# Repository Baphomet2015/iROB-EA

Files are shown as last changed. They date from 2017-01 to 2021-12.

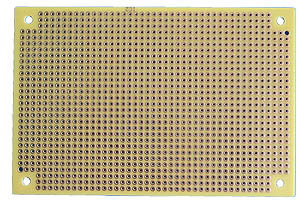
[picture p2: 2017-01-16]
Doc/Documentacion/Ilustraciones/wrapping_04.jpg

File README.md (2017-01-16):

# iROB-EA
Proyecto de Robot Movil Autónomo

Se trata de un Robot Móvil Autónomo todo terreno para exploración de entornos abiertos.

Dos modos básicos de funcionamiento:

 1. Modo autónomo con capacidad de ejecutar tareas de exploración programadas.
 
 2. Modo guiado recibiendo instrucciones en remoto.

Está equipado entre otros con los siguientes sensores:

 1. Estación Meteorológica.
 2. Sensores de Temperatura por infrarrojos.
 3. Sensores de ultrasonidos.
 4. Acelerómetro, brújula, sensores de posicion X-Y-Z.
 5. Camara video HD , movimiento X-Y.
 6. Microfonos.
 7. GPS

Conectividad y Sw básico:

 1. Conectividad Internet.
 2. Servidor web embebido.

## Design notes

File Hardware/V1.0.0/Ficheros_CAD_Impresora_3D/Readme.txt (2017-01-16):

Notas sobre el diseño de las piezas CAD utilizadas en iROB-EA

1) Para el diseño de estas piezas se ha utilizado el software FreecAD.

Descarga:	http://www.freecadweb.org/
Tutorial:	http://spainlabs.com/wiki/index.php?title=Tutorial_r%C3%A1pido_de_FreeCad
		http://www.iearobotics.com/wiki/index.php?title=Dise%C3%B1o_de_piezas_con_Freecad

2) Para la impresion de las piezas se ha utilizado una impresora 3D xyzprinting, modelo da Vinci 1.0.A

Web:		http://www.xyzprinting.com
Producto:	http://us.xyzprinting.com/us_es/Product/da-Vinci-1.0

Todas las piezas se han impreso utilizando como material de impresión plástico, PLA.

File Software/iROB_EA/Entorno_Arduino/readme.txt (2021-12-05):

iROB-EA, Librerías específicas Arduino del proyecto

LIBRERIAS

las carpetas contenidas en este directorio contienen las librerias especificas y 
necesarias para compilar la aplicación que se ejecuta en el Arduino MEGA2560.
Se deben copiar tal cual estan en el directorio "libraries" de la versión de IDE Arduino
que se esté utilizando.

Atención:
Es posible que alguna de estas librerias Ya exista en el directorio de "libraries" del IDE,
en cuyo caso es recomendable reemplazar la que exista por la que se encuentra aquí.

ENTORNO ARDUINO

La versión del IDE de Arduino con la que se ha desarrollado el SW es la 1.8.12

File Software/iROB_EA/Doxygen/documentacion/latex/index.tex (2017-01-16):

Proyecto\+: i\+R\+O\+B-\/\+EA 

\begin{DoxyDate}{Date}
Fecha\+: Abril 2015 
\end{DoxyDate}
\begin{DoxyAuthor}{Author}
A\+AL
\end{DoxyAuthor}
\begin{DoxyRemark}{Remarks}
Hardware Arduino M\+E\+GA 2560~\newline
 
\end{DoxyRemark}
\begin{DoxyVersion}{Version}
Versión de SW 1.\+0 

Versión de I\+DE Arduino\+: 1.\+6.\+4
\end{DoxyVersion}
{\bfseries Leitmotiv\+:}~\newline
 \char`\"{}\+Toda Bestia necesita un Cerebro...\char`\"{}, Dr. Frankenstein, en su laboratorio~\newline
 \char`\"{}¡\+Larga y próspera vida!.\char`\"{}, Sr. Spock~\newline

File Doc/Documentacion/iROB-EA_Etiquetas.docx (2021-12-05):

CN1 CN1 CN1 CN2 CN2 CN2 CN3 CN3 CN3 CN4 CN4 CN4 CN5 CN5 CN5 CN6 CN6 CN6 | CN7 CN7 CN7 CN8 CN8 CN8 CN9 CN9 CN9 CN10 CN10 CN10 CN11 CN11 CN11 CN12 CN12 CN12
CN13 CN13 CN13 CN14 CN14 CN14 CN15 CN15 CN15 CN16 CN16 CN16 CN17 CN17 CN17 CN18 CN18 CN18 | CN19 CN19 CN19 CN20 CN20 CN20 CN21 CN21 CN21 CN22 CN22 CN22 CN23 CN23 CN23 CN24 CN24 CN24
+ CN16 - - CN17 + + CN16 - - CN17 + P N P N | +12VDC ◄-- RS-232 Depuración USB programación
RX1 RX2 RX3 RX4 TX1 TX2 TX3 TX4 X Y SRVX SRVX X Y SRVY SRVY | U1 U1 U1 U4 U2 U2 U3 U3 U3 U4 U4 U4 U5 U5 U5
P1 P2 P3 P4 P1 P2 P3 P4 P1 P2 P3 P4 P1 P2 P3 P4 P1 P2 P3 P4 | U6 U6 U6 U7 U7 U7 U8 U8 U8 U9 U9 U9 U10 U10 U10
U11 U11 U11 U12 U12 U12 U13 U13 U13 U14 U14 U14 U15 U15 U15 | CARGADOR FIRMWARE 9DOF Razor IMU •GND

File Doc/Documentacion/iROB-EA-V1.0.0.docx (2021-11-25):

# xx

aAL

Versión 1.0, ENERO 2021

# 1 índice

# 2 objetivo

El objeto de este documento es describir un robot autónomo explorador que se denominará a lo largo de todo el documento iROB-EA.

## 2.1 glosario de términos

- iROB-EA. internet ROBobot Explorador Autónomo. Robot descrito en el presente documento.
- UF_xxx. Unidad Funcional.

El término concreto será del tipo UF_xxx dónde “xxx” serán tres caracteres alfanuméricos que identifican la Unidad Funcional.

- SS_xxx. Sub Sistema.

El término concreto será del tipo SS_xxx dónde “xxx” serán tres caracteres alfanuméricos que identifican el Subsistema.

# 3 introducción

Se propone el diseño de un robot autónomo cuya misión será explorar y recabar información del entorno que le rodea.

A lo largo del presente documento se aportará toda la información necesaria para comprender el funcionamiento del iROB-EA así como para su construcción a nivel hardware, en tanto que la información relacionada con el software necesario para su correcto funcionamiento se encuentra fuera de este documento, formando parte de la documentación general del proyecto.

Así mismo, si bien este documento recoge la documentación de detalle del hardware del iROB-EA la construcción “final” del mismo queda a la elección del lector, por lo que no se darán indicaciones de cómo se debe construir una parte concreta u otra, si el lector decide por ejemplo utilizar un chasis de otro tipo quedará pues a su elección.

# 4 especificaciones

Se definen las siguientes especificaciones para el iROB-EA.

# 5 arquitectura

En este capítulo se recoge la arquitectura del iROB-EA.

La Arquitectura del iROB-EA se estructura en base a xx Unidades Funcionales (UFs).

Cada una de estas unidades está a su vez formada por varios Subsistemas que tienen relación directa entre ellos, estos subsistemas en conjunto proveen la funcionalidad que la UF soporta.

Un subsistema debe ser entendido como un circuito o conjunto de ellos que operan bien de forma autónoma o controlados por una aplicación o software.

Algunos subsistemas son simples circuitos mientras que otros pueden tener más entidad.

La siguiente ilustración muestra las distintas UFs que conforman la arquitectura y su relación entre ellas.

Ilustración 1. Arquitectura iROB-EA.

Como se puede apreciar existen xx UFs claramente diferenciadas cuya misión se describe a continuación.

## 5.1 UF_SYS

Unidad Funcional de SYStema.

Esta UF es la encargada de proveer los siguientes servicios:

- Gestión de sensores.
- Gestión de actuadores.
- Interfaz de depuración (debug).
- Gestión de alimentación subsistemas.
- Implementación del mecanismo de reacciones básicas.

Esta UF implementa el “BIOS” del iROB-EA soportando todas las funciones de bajo nivel tales como gestión de sensores y actuadores, obteniendo de los mismos la información que facilitan y poniéndola a disposición de la UF_APL que es la encargada de ejecutar los programas y aplicaciones de alto nivel del iROB-EA.

Una tarea importante llevada a cabo en esta UF es la de soportar un mecanismo denominado de reacciones básicas, por el cual la UF_SYS responde de forma automática ante determinadas situaciones reconocidas en base a la información obtenida de los diferentes sensores. Este mecanismo funciona de forma similar al que provoca los actos reflejos en los seres vivos.

Existen situaciones de alta prioridad ante las que es preciso actuar de forma inmediata dado que son potencialmente peligrosas para la integridad del iROB-EA, ante cualquiera de estas situaciones la UF_SYS procede a asegurar la integridad del iROB-EA para posteriormente comunicar la aparición de esta situación a la UF_APL.

La UF_SYS está formada por un único subsistema:

- SS_SYS. Subsistema principal de la UF_SYS.

### 5.1.1 SS_SYS

Este subsistema es el único componente de la UF_SYS y está implementado entorno a un Arduino MEGA2560,

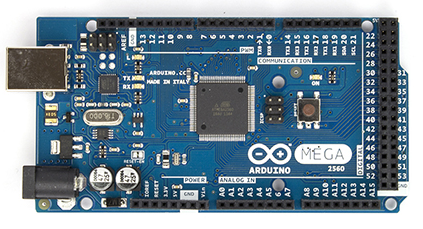
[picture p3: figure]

El modelo MEGA2560 posee entre otras, las siguientes características,

Microcontrolador | ATmega2560
Tensión de operación | 5V
Digital I/O Pins | 54 (15 de ellos soportan salida PWM)
Analógicos I/O Pins | 16
Corriente DC por I/O | 40 mA
Memoria Flash | 256 KB (8 KB usados por el bootloader)
SRAM | 8 KB
EEPROM | 4 KB
Clock | 16 MHz

Para más información consultar la web del fabricante,

http://arduino.cc/en/Main/ArduinoBoardMega2560

Así mismo se encuentra disponible en numerosos sitios online, entre otros,

http://tienda.bricogeek.com/arduino/306-arduino-mega-2560.html

https://www.sparkfun.com/products/11061

http://www.cooking-hacks.com/arduino-mega-2560

Como se ha comentado, este subsistema es el encargado de gestionar todos los sensores y actuadores del iROB-EA.

Este subsistema se comunica utilizando los puertos serie que incorpora el ArduinoMEGA2560 manteniendo conexión con los siguientes elementos:

- Exterior.

Puerto de comunicación serie RS-232 con el exterior para tareas de depuración y test, este puerto está presente en el conector exterior de DEBUG, soportado a través del SS_DBG de la unidad funcional UF_ENE, que convierte los niveles de Transmisión/Recepción a RS-232.

- UF_APL.

Puerto de comunicación serie con la UF_APL que es la unidad funcional encargada de ejecutar las aplicaciones que proveen de funcionalidad al iROB-EA.

## 5.2 UF_APL

Unidad Funcional de APLicaciones.

Esta UF es la encargada de proveer los siguientes servicios:

- xx
- xx
- xx

La UF_APL está formada por los siguientes subsistemas:

- xx
- xx
- xx

## 5.3 UF_ENE

Unidad Funcional de ENErgía.

Esta UF es la encargada de proveer los siguientes servicios:

- Encendido y Apagado general del iROB-EA.
- Recarga de baterías y obtención de información acerca del estado general de las mismas.
- Encendido y apagado de elementos y subsistemas.
- Alimentación y comunicaciones en modo pruebas (DEBUG).
- Watchdog.

La UF_ENE está formada por los siguientes subsistemas:

- SS_POW. Este subsistema es el encargado del encendido y apagado (power On/Off) del iROB-EA.
- SS_BAT. Este subsistema permite generar las tensiones de alimentación, recargar las baterías y operaciones asociadas con las mismas.
- SS_CNX. Subsistema que permite activar/desactivar la alimentación suministrada a distintos elementos del iROB-EA.
- SS_DBG. Subsistema encargado de soportar la depuración exterior
- SS_DOG. Subsistema WatchDog.

### 5.3.1 SS_POW

Este subsistema es el encargado del encendido y apagado del iROB-EA.

#### 5.3.1.1 Procedimiento de encendido (Power-ON).

El iROB-EA solo puede ser encendido utilizando el pulsador “power ON/OFF”, al hacerlo se iniciará el proceso de encendido (siempre que las baterías tengan energía suficiente).

Una vez presionado el pulsador de encendido y tras inicializarse correctamente el Arduino MEGA (algunos segundos) el display multifunción mostrará un mensaje indicando “espera de código de inicio” en ese momento se deberá generar el código de 4 dígitos necesario para la activación efectiva del iROB-EA.

Este código está formado por una secuencia de 4 dígitos que se envía al iROB-EA en forma de tonos multifrecuencia (DTMF) que pueden ser generados desde cualquier teclado de un teléfono convencional o dispositivo generador de tonos multifrecuencia DTMF compatible, para ello bastará acercar a cualquiera de los micrófonos del iROB-EA el elemento emisor y generar los tonos correspondientes a la clave de encendido.

Se dispone de xx segundos para enviar los 4 tonos, pasado ese tiempo el iROB-EA se apagará automáticamente.

Si la secuencia es correcta, el iROB-EA pasará al modo activo, en caso contrario se dispone de dos intentos más, agotados los cuales el iROB-EA pasará al modo de protección contra inicios incorrectos bloqueándose de forma permanente.

Importante:

Llegados a este punto, si se produce el bloqueo del iROB-EA, será necesario modificar en el código del programa fuente que ejecuta el Arduino MEGA, la constante que define la clave de arranque, definiendo otra distinta a la que exista, realizar una nueva compilación y cargar la nueva versión en el Arduino MEGA, esto conllevará entre otras cosas estar en disposición de los ficheros fuente con el código que ejecuta el Arduino MEGA para poder efectuar los cambios y generar una nueva versión.

Si la secuencia introducida es correcta el display multifunción mostrará un mensaje indicativo y el Arduino MEGA completará la secuencia de encendido, pasando al modo operativo.

#### 5.3.1.2 Procedimiento de apagado (Power-OFF).

Para el apagado del iROB-EA existen dos posibilidades:

- Apagado “físico”.

Esto es, utilizando de nuevo el pulsador “power ON/OFF”, se deberá mantener pulsado el mismo durante al menos xx segundos para confirmar el apagado.

- Apagado “remoto”.

Existe la posibilidad de apagar el iROB-EA en modo remoto, desde la interfaz web de control.

Hay que tener en cuenta que si se utiliza esta modalidad de apagado, el iROB-EA quedará totalmente fuera de servicio, siendo preciso el encendido del mismo utilizando de nuevo el pulsador “power ON/OFF”.

En ambos casos el display multifunción mostrará un mensaje indicando que se está realizando el proceso de apagado. Las operaciones de apagado son realizadas por el Arduino MEGA y conllevan el apagado “ordenado” de los diferentes módulos, así por ejemplo la UF_APL no puede ser desconectada “sin más” puesto que en caso de estar activa es preciso que se cierren todas las aplicaciones que estuvieran ejecutándose antes de proceder a su desconexión física. Finalmente se desconectará la alimentación general de todo el sistema.

### 5.3.2 SS_BAT

Este subsistema permite generar las tensiones de alimentación de los diferentes elementos, recargar las baterías y obtener información relacionada con las baterías.

En el diseño del iROB-EA se ha considerado prioritario unificar las distintas tensiones a utilizar en los circuitos de cara a reducir la complejidad de los circuitos necesarios para generarlas, así como optimizar el espacio ocupado por elementos como baterías, reguladores etc.

El resultado es la utilización de tres únicas tensiones:

### 5.3.3 SS_CNX

Este subsistema permite activar/desactivar la alimentación suministrada a distintos elementos del iROB-EA.

Algunos elementos del iROB-EA pueden ser alimentados o no, dependiendo si son necesarios, esto permite gestionar y el consumo de los mismos, optimizando así el consumo general del sistema.

Un ejemplo típico de esta circunstancia es la cámara IP, efectivamente, se trata de un elemento que presenta un consumo significativo y que no es necesario tener alimentado permanentemente.

Los elementos que pueden activarse/desactivarse desde este subsistema son:

- Cámara de vídeo.
- Módulo de GPS.
- Luces.
- Sensores de consumo elevado.
- Raspberry (Máquina Linux).

Estos elementos se conectan /desconectan siempre desde el Arduino que es el sistema que determina qué elementos deben estar funcionando en todo momento.

La conexión/desconexión de los diferentes elementos se realiza utilizando relés de enclavamiento, este tipo de relés tienen como principal ventaja la de no precisar alimentación permanente mientras están activados, por el contrario precisan de dos señales para su maniobra, (una para abrir los contactos y otra para cerrarlos) dado que en el Robot uno de los requisitos más importantes es el del consumo, se ha optado por implementar este subsistema con este tipo de relés.

### 5.3.4 SS_DBG

Subsistema de depuración del iROB-EA (Modo DEBUG).

El iROB-EA posee un conector exterior que permite realizar tareas de comprobación y depuración, este conector permite además alimentar el iROB-EA exteriormente lo cual es especialmente útil cuando se realizan tareas de mantenimiento, supervisión, pruebas etc dado que evita la utilización de las baterías en estos momentos.

Este subsistema “desconecta” automáticamente las baterías y alimenta todos los circuitos directamente desde las alimentaciones que se suministran a través del conector.

Para efectuar la comunicación con el exterior, el SS_DBG comunica el Arduino MEGA con el exterior mediante uno de sus puertos serie, los niveles lógicos de este puerto (TX, RX) son enviados y recibidos del exterior a través de un driver RS-232 que hace que la comunicación se más robusta y fiable, pudiendo alcanzar mayores distancias que con los niveles lógicos TTL.

### 5.3.5 SS_DOG.

Este subsistema implementa dos servicios:

- Master Reset.

Señal de reset maestro, se utiliza para inicializar el Arduino y aquellos elementos que precisen ser inicializados en el momento del arranque del iROB-EA.

- WatchDog.

El término WatchDog hace referencia a un circuito que de forma independiente es capaz de generar un pulso cada cierto tiempo si antes no recibe una señal de control.

El uso típico de este tipo de circuitos es el de “resetear” un sistema cuando este ha perdido el control y no responde (sistemas basados en software, microcontroladores, ordenadores etc).

Es importante destacar que el Arduino MEGA tiene implementado un sistema de watchdog pero de la documentación existente se desprende que es preciso modificar el bootloader que incorpora de fábrica para habilitar este watchdog, además de las fuentes consultadas se desprende que en determinados casos podría producirse algún tipo de funcionamiento no deseado por lo que se ha optado por implementar un sistema de watchdog externo al Arduino MEGA.

El SS_DOG generará un pulso de Master Reset automáticamente si no recibe una señal de control periódica generada en este caso desde el Arduino MEGA.

La generación del pulso de Master Reset es configurable mediante unos puentes, pudiendo elegirse entre 1 y 64 segundos.

## 5.4 UF_MOT

Unidad Funcional de MOTores.

El iROB-EA cuenta con dos motores de CC que son los encargados de relazar el movimiento, cada uno de ellos está asociado a cada una las orugas, derecha e izquierda.

Mediante el accionamiento de estos motores es posible realizar los movimientos necesarios para desplazar / girar el iROB-EA.

Esta UF es la encargada de proveer los siguientes servicios:

- Movimiento del iROB-EA.
- Monitorización de los motores de propulsión.

La UF_MOT está formada por los siguientes subsistemas:

- SS_MOT. Este subsistema es el encargado del control de los motores y realiza las tareas relacionadas con el movimiento del iROB-EA:
  - Avance
  - Retroceso
  - Giro derecha
  - Giro Izquierda
- SS_MSE. Este subsistema permite monitorizar el estado de ambos motores.

### 5.4.1 SS_MOT

Este subsistema gira entorno a dos motores de CC que permiten realizar todos los movimientos del iROB-EA.

Cada uno de los motores está operado por un controlador independiente que recibe las señales de control del Arduino MEGA.

### 5.4.2 SS_MSE

Como se ha indicado al describir el SS_MOT, cada uno de los motores está operado por un controlador independiente, estos controladores además proporcionan al sistema de control una serie de señales que permite monitorizar el estado del motor controlado.

Adicionalmente se ha añadido a cada uno de los controladores un sensor de corriente que permite monitorizar el consumo de cada motor. La monitorización de la corriente consumida por cada motor es especialmente importante dado que permite detectar averías y bloqueos del motor durante su funcionamiento.

# 6 diseño detallado

Este capítulo recoge la información precisa para la construcción del iROB-EA.

## 6.1 consideraciones previas

Antes de abordar en detalle la descripción de los diferentes subsistemas es necesario hacer las siguientes consideraciones:

Para la construcción de los circuitos se ha optado por la técnica de wire-wrap, por lo que no se ha recurrido a la fabricación de circuitos impresos.

Esta técnica es ideal para prototipado y dado que el Robot descrito en este documento lo es, se ha considerado una solución ideal para la construcción del mismo.

Par más información sobre esta técnica de construcción se puede consultar,

http://es.wikipedia.org/wiki/Wire-wrap

La técnica de wire-wrap aporta entre otras las siguientes ventajas frente a la utilización de circuitos impresos “clásicos”:

- Facilidad y mayor flexibilidad para introducir cambios en el diseño, no siendo necesariamente precisa la fabricación de nuevos circuitos impresos, ante modificaciones en el diseño.
- Robustez y fiabilidad, permitiendo aprovechar al máximo el espacio en circuitos complejos (uso de buses y conexiones numerosas).

Por el contrario la técnica de wrapping requiere:

- Herramientas especiales (a menudo caras), necesarias para realizar las conexiones y la utilización de hilo específico (AWG20) para efectuarlas.
- Componentes adicionales como hileras de pines de diversos tipos para efectuar el wrapping de los hilos.
- Utilización de tarjetas de prototipado multi taladradas.

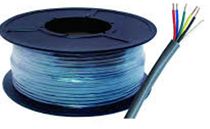
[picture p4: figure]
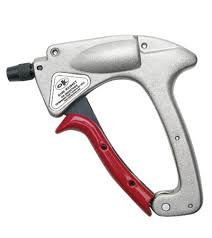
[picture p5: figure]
wrapping_01
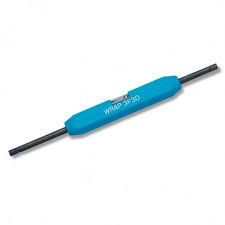
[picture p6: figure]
wrapping_03
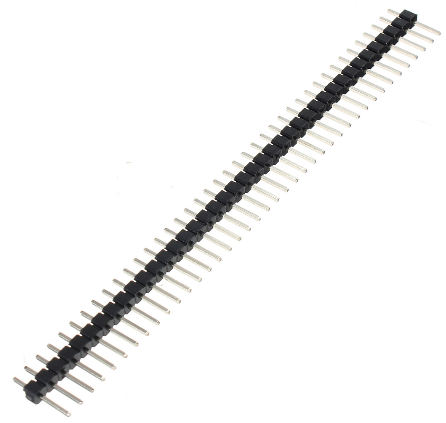
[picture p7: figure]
wrapping_04

Estas desventajas se traducen finalmente en un coste final más elevado, si bien la ventaja de poder efectuar cambios en el diseño suple con creces la mayor inversión en la implementación.

## 6.2 uf_ene

Unidad Funcional de ENErgía.

Seguidamente se describen en detalle los subsistemas que forman esta UF.

### 6.2.1 ss_pow

### 6.2.2 ss_cnx

### 6.2.3 ss_bat

### 6.2.4 ss_dbg

### 6.2.5 ss_dog

## 6.3 UF_MOT

Unidad Funcional de MOTores.

Seguidamente se describen en detalle los subsistemas que forman esta UF.

### 6.3.1 SS_MOT

### 6.3.2 SS_MSE

# 7 descripción de conectores

Este capítulo detalla los diferentes conectores que conexionan los distintos circuitos y módulos del iROB-EA.

- Conector CN01

Monitorización de carga de batería y señal de encendido (Power ON) de la batería.

CN_01 | TIPO:
PIN | NOMBRE | DESCRIPCIÓN
1 | GND | GND
2 | BAT-N100 | Test 100% Carga
3 | BAT-N75 | Test 75% Carga
4 | BAT-N50 | Test 50% Carga
5 | BAT-25 | Test 25% Carga
6 | CTRL-ON-OFF | Pulsador de encendido de la Batería

- Conector CN02

Control de los relés de alimentación, obtención de alimentaciones generales del Robot y señal de petición de apagado.

CN_02 | TIPO:
PIN | NOMBRE | DESCRIPCIÓN
1 | GND | GND
2 | +5VA | +5V, Alimentación General, Robot
3 | +3.3VA | +3.3V, Alimentación General, Robot
4 | POWER-CNX-A0
5 | POWER-CNX-A1
6 | POWER-CNX-A2
7 | DEBUG-ACTIVO
8 | POWER-OFF-PETICION
9 | ICC-SENSE-5VP
10 | ICC-SENSE-12P

CN_03 | TIPO:
PIN | NOMBRE | DESCRIPCIÓN
1 | +12V_DEBUG | +12V, Alimentación para pruebas
2 | GND_DEBUG | GND, Alimentación para pruebas
3 | +5V_DEBUG | +5V, Alimentación para pruebas

CN_04 | TIPO:
PIN | NOMBRE | DESCRIPCIÓN
1 | OUT12V_VCC | +12V, salida de la Bateria
2 | OUT5V_GND | GND, salida de la Bateria
3 | OUT5V_VCC | +5V, salida de la Bateria

CN_05 | TIPO:
PIN | NOMBRE | DESCRIPCIÓN
1 | +12P | +12V, Foco led Camara
2 | +12P | +12V, Alimentación motores

CN_06 | TIPO:
PIN | NOMBRE | DESCRIPCIÓN
1 | GND | GND
2 | +5VP | +5V, Alimentación PC

CN_07 | TIPO:
PIN | NOMBRE | DESCRIPCIÓN
1 | GND | GND
2 | POWER ON/OFF | Pulsador ON/OFF
3 | PULSADOR-ON-OFF | Pulsador de encendido de la Batería

CN_08 | TIPO:
PIN | NOMBRE | DESCRIPCIÓN
1 | +5V | +5V, Alimentación General, Robot
2 | GND | GND
3 | +12V | +12V, Alimentación General, Robot
4 | DEBUG-ACTIVO | Señal de conector enchufado

CN_09 | TIPO:
PIN | NOMBRE | DESCRIPCIÓN
1 | +5V | +5V, Alimentación General, Robot
2 | GND | GND
3 | MICROFONO | MICROFONO
4 | HCMS-DATA-IN | DISPLAY HCMS-2963
5 | HCMS-RS | DISPLAY HCMS-2963
6 | HCMS-CLK | DISPLAY HCMS-2963
7 | HCMS-RESET | DISPLAY HCMS-2963
8 | HCMS-CE | DISPLAY HCMS-2963

CN_10 | TIPO:
PIN | NOMBRE | DESCRIPCIÓN
1 | POWER ON/OFF | Pulsador ON/OFF
2 | GND | GND
3 | GND | GND
4 | +5V | +5V, Alimentación General, Robot

CN_11 | TIPO:
PIN | NOMBRE | DESCRIPCIÓN
1 | POW-PC-1 | Pulsador encendido PC
2 | POW-PC-2 (GND) | Pulsador encendido PC

CN_12 | TIPO:
PIN | NOMBRE | DESCRIPCIÓN
1 | GND | GND
2 | GPS-TX | GPS, TX
3 | GPS-RX | GPS, RX
4 | +5VA | +5V, Alimentación General, Robot

CN_13 | TIPO:
PIN | NOMBRE | DESCRIPCIÓN
1 | GND | GND
2 | LEDS-IZQ | Leds delanteros, izquierdo
3 | LEDS-DER | Leds delanteros, derecho

CN_14 | TIPO:
PIN | NOMBRE | DESCRIPCIÓN
1 | SE-SUELO | Salida sensor suelo
2 | GND | GND
3 | +5VA | +5V, Alimentación General, Robot

CN_15 | TIPO:
PIN | NOMBRE | DESCRIPCIÓN
1 | 3V3 | Salida del regulador interno del adaptador, NO ESTÁ UNIDA con los +3.3V, Alimentación General, Robot
2 | PC-TX | TX, USB PC
3 | PC-RX | RX, USB PC
4 | GND | GND
5 | +5V | NO ESTÁ UNIDA con los +5V, Alimentación General, Robot

CN_16 | TIPO:
PIN | NOMBRE | DESCRIPCIÓN
1 | M1 | Motor derecho +
2 | M2 | Motor derecho -

CN_17 | TIPO:
PIN | NOMBRE | DESCRIPCIÓN
1 | M1 | Motor izquierdo +
2 | M2 | Motor izquierdo -

CN_18 | TIPO:
PIN | NOMBRE | DESCRIPCIÓN
1 | GND | GND
2 | TX | DBG-RS232-TX
3 | RX | DBG-RS232-RX

CN_19 | TIPO:
PIN | NOMBRE | DESCRIPCIÓN
1 | ALS-PT19 | Salida sensor luz
2 | CAM-SERVO-X | Servo horizontal, movimiento cámara
3 | CAM-SERVO-Y | Servo vertical, movimiento cámara
4 | +3.3VA | +3.3V, Alimentación General, Robot
5 | +5VA | +5V, Alimentación General, Robot
6 | GND | GND
7 | SCL-3.3V | SCL, Niveles de +3.3V !!
8 | SDA-3.3V | SDA, Niveles de +3.3V !!
9 | FAN | ON/OFF del ventilador
10 | SQW | Señal SQW del RTC, Niveles de +3.3 !!

CN_20 | TIPO:
PIN | NOMBRE | DESCRIPCIÓN
1 | +5VA | +5V, Alimentación General, Robot
2 | GND | GND
3 | CAM-SERVO-X | Servo horizontal, movimiento cámara
4 | CAM-SERVO-Y | Servo vertical, movimiento cámara
5 | WEATHER-MLX90614-SDA | SDA (ver esquema sparkfun para direcciones)
6 | WETAHER-MLX90614-SCL | SCL (ver esquema sparkfun para direcciones)

CN_21 | TIPO:
PIN | NOMBRE | DESCRIPCIÓN
1 | GND | GND
2 | +3.3VA | +3.3V, Alimentación General, Robot
3 | SCL-3.3V | SCL, Niveles de +3.3V !!
4 | SDA-3.3V | SDA, Niveles de +3.3V !!
5 | SQW | Señal SQW del RTC

CN_22 | TIPO:
PIN | NOMBRE | DESCRIPCIÓN
1 | RX | Interruptor RX
2 | RX | Interruptor RX
3 | TX | Interruptor TX
4 | TX | Interruptor TX

Conector externo de DEBUG

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
CN_DEBUG | TIPO:
PIN | COLOR | NOMBRE | DESCRIPCIÓN
1 | Blanco | D- | USB, programación de Arduino, Datos -
2 | Azul | RX | RS-232, recepción, puerto de comunicación externo con Arduino
3 | Verde | TX | RS-232, transmisión, puerto de comunicación externo con Arduino
4 | Malla | GND | GND y malla del cable
5 | Rosa y Gris | +5V | Alimentación general, +5V
6 | Amarillo | D+ | USB, programación de Arduino, Datos +
7 | Rojo y Marrón | +12V | Alimentación general, +12V

# 8 anexo

## 8.1 tabla de asignación de pines en arduino mega2560.

Resumen de asignación de pines en Arduino MEGA.

Asignación de Pines I/O
FUNCIONALIDAD | PINES I/O | TIPO | ASIGNACIÓN
| | | PIN | NOMBRE | MODO

CONTROL LEDS
Leds rojos (posición) | 1 | Digital: 1 | D37 | LEDS-POS | O
Leds blancos derechos | 1 | Digital: 1 | D38 | LEDS-DER | O
Leds blancos izquierdos | 1 | Digital: 1 | D39 | LEDS-IZQ | O
Foco Led Cámara | 1 | Digital: 1 | D9 | FOCO_LED | O

APAGADO GENERAL DEL ROBOT
Señal de petición de apagado general del Robot | 1 | Digital: 1 | D02 | POWER-OFF_PETICION | I (INT0 del Arduino MEGA2560)

DISPLAY HCMS2963
Display multifunción HCMS2963 | 5 | Digital: 5 | D40 D41 D42 D43 D44 | HCMS-RESET HCMS-RS HCMS-CE HCMS-CLK HCMS-DATA-IN | O O O O O

CONTROL MOTORES
Motor derecho | 3 | Digital: 3 | D4 D31 D30 | MTD-PWM MTD-RESET MTD-DIR | O O O
Motor izquierdo | 3 | Digital: 3 | D5 D29 D28 | MTI-PWM MTI-RESET MTI-DIR | O O O

MULTIPLEXOR DE LECTURA, SEÑALES DE ESTADO DE MOTORES
Multiplexor para leer el estado de los motores, la señal a leer se obtiene en MTDI-INFO MTDI-SEL-C MTDI-SEL-B MTDI-SEL-A OPERACIÓN 0 0 0 Sense I, motor derecho 0 0 1 FF2, motor derecho 0 1 0 FF1, motor derecho 0 1 1 Sense I, motor izquierdo 1 0 0 FF2, motor izquierdo 1 0 1 FF1, motor izquierdo 1 1 0 GND (0V) 1 1 1 GND (0V) | 4 | Digital: 3 Analógico: 1 | D25 D26 D27 A3 | MTDI-SEL-C MTDI-SEL-B MTDI-SEL-A MTDI-INFO | O O O I

SENSOR SUELO
Sensor delantero de detección de suelo | 1 | Digital: 1 | A2 | SE-SUELO | I

ESTACIÓN METEOROLÓGICA
Sensores HTU21D / MPL3115A2 / MLX90614 | 1 | SDA | I2C Niveles 3.3V | SDA-3.3V | O
| 1 | SCL | | SCL-3.3V | I
Sensor luz ambiente | 1 | Analógico: 1 | A1 | ALS-PT19 | I
Ventilador para forzado de aire | 1 | Digital: 1 | D8 | FAN | O

MÓDULO 9DOF-Razor-v21
Módulo 9DOF-Razor-v21 (acelerómetro, giroscopio, magnetómetro) http://blog.bricogeek.com/noticias/tutoriales/imu-razor-9-dof-con-ahrs-y-conexion-usb/ | 2 | Puerto Serie | TX2 RX2 | | O I
Módulo 9DOF-Razor-v21 (acelerómetro, giroscopio, magnetómetro), señal DTR | 1 | Digital: 1 | -- | | O

PUERTO DEPURACIÓN (DEBUG)
Puerto exterior para depuración ATENCIÓN: Interfaz RS-232 utilizando MAX232, niveles lógicos de RS-232, ±12V Señal que indica que se ha conectado el conector de DEBUG | 2 1 | Puerto serie Digital: 1 | TX3 RX3 D53 | DEBUG-ACTIVO | O I I

MÓDULO GPS GY-NEOMV2
GPS GY-NEOMV2 | 2 | Puerto Serie | TX1 RX1 | | O I

PUERTO COMUNICACIÓN ARDUINO-PC
Puerto serie de comunicación entre el PC y el Arduino. En el extremo PC incorpora un adaptador USB-SERIE | 2 | Puerto Serie | TX0 RX0 | | O I

DECODIFICADOR DE TONOS DTMF
Decodificador tonos DTMF (75T2090) | 6 | Digital: 5 Analógico: 1 | D52 D51 D50 D49 D48 A0 | 75T2090, D3 75T2090, D2 75T2090, D1 75T2090, D0 75T2090, DV 75T2090, DIN Entrada señal (salida del micrófono), También se envía a A0 | I I I I I I

DECODIFICADOR CONTROL DE RELÉS
Decodificador de control de ON/OFF de los relés, activación/desactivación alimentación del PC y motores. POWER-CNX-A2 POWER-CNX-A1 POWER-CNX-A0 OPERACIÓN 0 0 0 -- 0 0 1 ON +5VP PC 0 1 0 OFF +5VP PC 0 1 1 ON +12P 1 0 0 OFF +12P 1 0 1 OFF apagado ROBOT 1 1 0 -- 1 1 1 -- | 3 | Digital: 3 | D45 D46 D47 | POWER-CNX-A2 POWER-CNX-A1 POWER-CNX-A0 | O O O

NIVEL BATERIA
Nivel de batería: 25% Nivel de batería: 50% Nivel de batería: 75% Nivel de batería: 100% Estas señales son generadas desde la batería | 4 | Digital: 4 | D33 D34 D35 D36 | BAT-N25 BAT-N50 BAT-N75 BAT-N100 | I I I I

ENCENDIDO PC
Encendido del PC | 1 | Digital: 1 | D32 | POW-PC-1 | O

SENSORES CORRIENTE GENERALES
Sensor corriente +5VP, alimentación PC | 1 | Analógico: 1 | A5 | ICC-SENSE-5VP | I
Sensor corriente +12P, alimentación motores | 1 | Analógico: 1 | A4 | ICC-SENSE-12P | I

CONTROL SERVOS CÁMARA VIDEO
Control servo eje X, horizontal | 1 | Digital: 1 | D6 | CAM-SERVO-X | O
Control servo eje Y, vertical | 1 | Digital: 1 | D7 | CAM-SERVO-Y | O

SENSORES DE ULTRASONIDOS
Ultrasonidos derecho, trigger Ultrasonidos izquierdo, trigger Ultrasonidos derecho, ECHO Ultrasonidos izquierdo, ECHO | 4 | Digital: 4 | D13 | US-TRIG-DER | O
| | | D22 | US-TRIG-IZQ | O
| | | D23 | US-ECHO-DER | I
| | | D24 | US-ECHO-IZQ | I

## 8.2 RESÚMEN DE asignación de puertos serie en arduino mega2560.

FUNCIONALIDAD | PUERTO SERIE
PUERTO COMUNICACIÓN ARDUINO-PC Velocidad: 19200 | TX0
MÓDULO GPS GY-NEOMV2 Velocidad: | TX1
MÓDULO 9DOF-Razor-v21 Velocidad: | TX2
PUERTO DEPURACIÓN (DEBUG) Velocidad: 19200 | TX3

## 8.3 identificación de relés

Verde

RE1, Relé de alimentación PC.

Amarillo

RE2, Relé de control de encendido/apagado general del Robot.

Azul

RE3, Relé de alimentación de motores.

Rojo

RE2, Relé de control de encendido/apagado general del Robot.

Verde

RE5, Relé DEBUG, entrada de alimentación exterior desde el conector de DEBUG.

Amarillo

RE6, Relé de protección contra polaridad incorrecta, entrada de carga de la batería.

## 8.4 identificación de FUSIBLES

iROB-EA Documentación de desarrollo

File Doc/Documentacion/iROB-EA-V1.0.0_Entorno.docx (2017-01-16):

# xx

aAL

Versión 1.0.0, MARZO 2016

# 1 definición de entorno

Para poder compilar las aplicaciones y programas que se ejecutan en el iROB-EA se debe tener instalado y configurado el siguiente entorno:

La configuración descrita se ha probado con las versiones que se detallan, sin embargo es posible que por ejemplo utilizando un IDE de Arduino más moderno o una versión de Sublime más actualizada también funcione pero no está garantizado.

Importante:

La instalación descrita se ha efectuado en un PC con Windows 7.

## 1.1 entorno arduino

El hardware en que se basa el sistema de control del iROB-EA está basado en un Arduino MEGA2560.

Para complilar los sketches (programas) que ejecuta el Arduino MEGA2560 se ha utilizado:

- Editor Sublime Text versión 3, build 3103

Descarga: https://www.sublimetext.com/3

- Plugin Stino-master para Sublime Text

Descarga: https://github.com/Robot-Will/Stino/wiki/New-version-of-STino

Este plugin permite añadir a Sublime Text un menú con opciones de Arduino, es decir “enlaza” el IDE de Arduino con el propio sublime Text.

Para que este plugin funcione correctamente es preciso realizar las siguientes modificaciones después de instalarlo, (la instalación se efectúa siguiendo las instrucciones que se detallan en el sitio de descarga).

DESPUÉS de instalarlo en Sublime Text hay que configurar el directorio dónde está instalado el IDE de Arduino, utilizando la opción del nuevo menú que aparecerá en Sublime Text,

Arduino->Preferences->Select Arduino Aplicaction Folder

Finalmente hay que realizar estos ajustes:

1. Es necesario añadir unas líneas en el fichero arduino_target_params.py que se encuentra en la carpeta de instalación del Stino, dentro de sublime, en la opción:

Preferences->Browse Packages, carpeta Stino\stino\payarduino

Abrir el fichero indicado y buscar en el fichero la sección,

params['software'] = 'ARDUINO'

y añadir al final de la lista,

params['runtime.tools.avrdude.path'] = target_tools_avrdude_path

De igual forma justo encima de esta sección hay otra con líneas del tipo = os.path.join, hay que añadir aquí esta línea,

target_tools_avrdude_path = os.path.join(ide_path, 'hardware/tools/avr')

2. Añadir en la variable de entorno en Windows PATH la ruta dónde se encuentran las aplicaciones del IDE de Arduino, que se encontrarán en:

Directorio_Instalacion_Arduino\hardware\tools\avr\bin

Muy Importante:

Cuando se sube un skecth (programa) a una tarjeta Arduino desde Sublime Text (en este caso el MEGA2560) SIEMPRE al final dá un error de tipo “avrdude: stk500_getsync(): not in sync: resp=0x00” o algo parecido, esto es debido a que desde el plugin de Stino no se recoge correctamente la respuesta que envía el IDE de Arduino como confirmación de que se ha subido el programa a la tarjeta, pero se ha subido correctamente.

- IDE Arduino versión 1.6.4

Descarga: https://www.arduino.cc/en/Main/OldSoftwareReleases#previous

En el directorio de librerías del IDE de Arduino es necesario copiar todas las librerias específicas que se necesitan para el sketch que ejecuta el iROB-AE, estas liberías específicas se encuentran en el directorio del proyecto del iROB-EA,

Software\Entorno_Arduino

El directorio del IDE de arduino dónde se deben copiar las carpetas de las librerías espcíficas es,

Directorio_Instalacion_Arduino\libraries

Nota (1):

Es posible que alguna librería ya exista previamente en el directorio de librerías del IDE 1.6.4, en ese caso lo recomendable es sustituirla por la de este directorio del iROB-EA.

iROB-EA Documentación de desarrollo

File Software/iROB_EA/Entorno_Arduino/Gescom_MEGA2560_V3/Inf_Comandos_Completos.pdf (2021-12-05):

# GESCOM MEGA2560 V3

comandos: | 73

### LISTADO DE COMANDOS

versión generada: 2021/12/01 13:43

Gescom_MEGA2560_V3

String a enviar

B_PPAK | Bateria Power Pack | #####100101011010001
Parametro 1: | GV1 | Obtener Valor 1
Parametro 2: | NOP | Nada
Destino: | R00 | iROB-EA-00
Origen: | CTR | Sistema de Control
Funcion: | cmd_Comando_B_PPAK(&gd)

String a enviar

C_LEDS | Control de los Leds | #####100102020010005
Parametro 1: | LD1 | Leds Blancos Delanteros
Parametro 2: | _ON | Encender
Destino: | R00 | iROB-EA-00
Origen: | CTR | Sistema de Control
Funcion: | cmd_Comando_C_LEDS(&gd)

String a enviar

C_LEDS | Control de los Leds | #####100102020010004
Parametro 1: | LD1 | Leds Blancos Delanteros
Parametro 2: | OFF | Apagar
Destino: | R00 | iROB-EA-00
Origen: | CTR | Sistema de Control
Funcion: | cmd_Comando_C_LEDS(&gd)

String a enviar

C_LEDS | Control de los Leds | #####100102020020005
Parametro 1: | LD2 | Leds Rojos Traseros
Parametro 2: | _ON | Encender
Destino: | R00 | iROB-EA-00
Origen: | CTR | Sistema de Control
Funcion: | cmd_Comando_C_LEDS(&gd)

Gescom_MEGA2560_V3

String a enviar

C_LEDS | Control de los Leds | #####100102020020004
Parametro 1: | LD2 | Leds Rojos Traseros
Parametro 2: | OFF | Apagar
Destino: | R00 | iROB-EA-00
Origen: | CTR | Sistema de Control
Funcion: | cmd_Comando_C_LEDS(&gd)

String a enviar

C_LEDS | Control de los Leds | #####100102020030005
Parametro 1: | LD3 | Leds, Foco led de la camara
Parametro 2: | _ON | Encender
Destino: | R00 | iROB-EA-00
Origen: | CTR | Sistema de Control
Funcion: | cmd_Comando_C_LEDS(&gd)

String a enviar

C_LEDS | Control de los Leds | #####100102020030004
Parametro 1: | LD3 | Leds, Foco led de la camara
Parametro 2: | OFF | Apagar
Destino: | R00 | iROB-EA-00
Origen: | CTR | Sistema de Control
Funcion: | cmd_Comando_C_LEDS(&gd)

String a enviar

C_MDER | Control motor derecho | #####100103100070001
Parametro 1: | AVA | Avanzar
Parametro 2: | NOP | Nada
Destino: | R00 | iROB-EA-00
Origen: | CTR | Sistema de Control
Funcion: | cmd_Comando_C_MDER(&gd)

Gescom_MEGA2560_V3

String a enviar

C_MDER | Control motor derecho | #####100103100030001
Parametro 1: | STO | Detener
Parametro 2: | NOP | Nada
Destino: | R00 | iROB-EA-00
Origen: | CTR | Sistema de Control
Funcion: | cmd_Comando_C_MDER(&gd)

String a enviar

C_MDER | Control motor derecho | #####10010311001XXXX
Parametro 1: | SV1 | Establecer Valor 1
Parametro 2: | XXXX | XXXX representa la longitud en HEXADECIMAL del string que se envía
con el valor del parámetro.
El valor viene como string detras del ultimo caracter del comando
Destino: | R00 | iROB-EA-00
Origen: | CTR | Sistema de Control
Funcion: | cmd_Comando_C_MDER(&gd)

String a enviar

C_MDER | Control motor derecho | #####100103100060001
Parametro 1: | INI | Inicializar
Parametro 2: | NOP | Nada
Destino: | R00 | iROB-EA-00
Origen: | CTR | Sistema de Control
Funcion: | cmd_Comando_C_MDER(&gd)

String a enviar

C_MDER | Control motor derecho | #####100103111010001
Parametro 1: | GV1 | Obtener Valor 1
Parametro 2: | NOP | Nada
Destino: | R00 | iROB-EA-00
Origen: | CTR | Sistema de Control
Funcion: | cmd_Comando_C_MDER(&gd)

Gescom_MEGA2560_V3

String a enviar

C_MDER | Control motor derecho | #####100103100080001
Parametro 1: | RET | Retroceder
Parametro 2: | NOP | Nada
Destino: | R00 | iROB-EA-00
Origen: | CTR | Sistema de Control
Funcion: | cmd_Comando_C_MDER(&gd)

String a enviar

C_MIZQ | Control motor izquierdo | #####100103000070001
Parametro 1: | AVA | Avanzar
Parametro 2: | NOP | Nada
Destino: | R00 | iROB-EA-00
Origen: | CTR | Sistema de Control
Funcion: | cmd_Comando_C_MIZQ(&gd)

String a enviar

C_MIZQ | Control motor izquierdo | #####100103000030001
Parametro 1: | STO | Detener
Parametro 2: | NOP | Nada
Destino: | R00 | iROB-EA-00
Origen: | CTR | Sistema de Control
Funcion: | cmd_Comando_C_MIZQ(&gd)

String a enviar

C_MIZQ | Control motor izquierdo | #####10010301001XXXX
Parametro 1: | SV1 | Establecer Valor 1
Parametro 2: | XXXX | XXXX representa la longitud en HEXADECIMAL del string que se envía
con el valor del parámetro.
El valor viene como string detras del ultimo caracter del comando
Destino: | R00 | iROB-EA-00
Origen: | CTR | Sistema de Control
Funcion: | cmd_Comando_C_MIZQ(&gd)

Gescom_MEGA2560_V3

String a enviar

C_MIZQ | Control motor izquierdo | #####100103000060001
Parametro 1: | INI | Inicializar
Parametro 2: | NOP | Nada
Destino: | R00 | iROB-EA-00
Origen: | CTR | Sistema de Control
Funcion: | cmd_Comando_C_MIZQ(&gd)

String a enviar

C_MIZQ | Control motor izquierdo | #####100103011010001
Parametro 1: | GV1 | Obtener Valor 1
Parametro 2: | NOP | Nada
Destino: | R00 | iROB-EA-00
Origen: | CTR | Sistema de Control
Funcion: | cmd_Comando_C_MIZQ(&gd)

String a enviar

C_MIZQ | Control motor izquierdo | #####100103000080001
Parametro 1: | RET | Retroceder
Parametro 2: | NOP | Nada
Destino: | R00 | iROB-EA-00
Origen: | CTR | Sistema de Control
Funcion: | cmd_Comando_C_MIZQ(&gd)

String a enviar

C_RELE | Control de reles | #####100106050000005
Parametro 1: | 12P | Rele Alimentacion Motores
Parametro 2: | _ON | Encender
Destino: | R00 | iROB-EA-00
Origen: | CTR | Sistema de Control
Funcion: | cmd_Comando_C_RELE(&gd)

Gescom_MEGA2560_V3

String a enviar

C_RELE | Control de reles | #####100106050000004
Parametro 1: | 12P | Rele Alimentacion Motores
Parametro 2: | OFF | Apagar
Destino: | R00 | iROB-EA-00
Origen: | CTR | Sistema de Control
Funcion: | cmd_Comando_C_RELE(&gd)

String a enviar

C_RELE | Control de reles | #####100106050010005
Parametro 1: | 5VP | Rele Alimentacion PC
Parametro 2: | _ON | Encender
Destino: | R00 | iROB-EA-00
Origen: | CTR | Sistema de Control
Funcion: | cmd_Comando_C_RELE(&gd)

String a enviar

C_RELE | Control de reles | #####100106050010004
Parametro 1: | 5VP | Rele Alimentacion PC
Parametro 2: | OFF | Apagar
Destino: | R00 | iROB-EA-00
Origen: | CTR | Sistema de Control
Funcion: | cmd_Comando_C_RELE(&gd)

String a enviar

C_RMOV | Comando de movimiento | #####100103200070001
Parametro 1: | AVA | Avanzar
Parametro 2: | NOP | Nada
Destino: | R00 | iROB-EA-00
Origen: | CTR | Sistema de Control
Funcion: | cmd_Comando_C_RMOV(&gd)

Gescom_MEGA2560_V3

String a enviar

C_RMOV | Comando de movimiento | #####100103200030001
Parametro 1: | STO | Detener
Parametro 2: | NOP | Nada
Destino: | R00 | iROB-EA-00
Origen: | CTR | Sistema de Control
Funcion: | cmd_Comando_C_RMOV(&gd)

String a enviar

C_RMOV | Comando de movimiento | #####10010321001XXXX
Parametro 1: | SV1 | Establecer Valor 1
Parametro 2: | XXXX | XXXX representa la longitud en HEXADECIMAL del string que se envía
con el valor del parámetro.
El valor viene como string detras del ultimo caracter del comando
Destino: | R00 | iROB-EA-00
Origen: | CTR | Sistema de Control
Funcion: | cmd_Comando_C_RMOV(&gd)

String a enviar

C_RMOV | Comando de movimiento | #####1001032000A0001
Parametro 1: | GDE | Girar derecha
Parametro 2: | NOP | Nada
Destino: | R00 | iROB-EA-00
Origen: | CTR | Sistema de Control
Funcion: | cmd_Comando_C_RMOV(&gd)

String a enviar

C_RMOV | Comando de movimiento | #####100103200090001
Parametro 1: | GIZ | Girar Izquierda
Parametro 2: | NOP | Nada
Destino: | R00 | iROB-EA-00
Origen: | CTR | Sistema de Control
Funcion: | cmd_Comando_C_RMOV(&gd)

Gescom_MEGA2560_V3

String a enviar

C_RMOV | Comando de movimiento | #####100103200060001
Parametro 1: | INI | Inicializar
Parametro 2: | NOP | Nada
Destino: | R00 | iROB-EA-00
Origen: | CTR | Sistema de Control
Funcion: | cmd_Comando_C_RMOV(&gd)

String a enviar

C_RMOV | Comando de movimiento | #####100103200080001
Parametro 1: | RET | Retroceder
Parametro 2: | NOP | Nada
Destino: | R00 | iROB-EA-00
Origen: | CTR | Sistema de Control
Funcion: | cmd_Comando_C_RMOV(&gd)

String a enviar

C_SRVX | Control Servo camara eje X | #####10010401001XXXX
Parametro 1: | SV1 | Establecer Valor 1
Parametro 2: | XXXX | XXXX representa la longitud en HEXADECIMAL del string que se envía
con el valor del parámetro.
El valor viene como string detras del ultimo caracter del comando
Destino: | R00 | iROB-EA-00
Origen: | CTR | Sistema de Control
Funcion: | cmd_Comando_C_SRVX(&gd)

String a enviar

C_SRVX | Control Servo camara eje X | #####100104000060001
Parametro 1: | INI | Inicializar
Parametro 2: | NOP | Nada
Destino: | R00 | iROB-EA-00
Origen: | CTR | Sistema de Control
Funcion: | cmd_Comando_C_SRVX(&gd)

Gescom_MEGA2560_V3

String a enviar

C_SRVY | Control Servo camara eje Y | #####10010411001XXXX
Parametro 1: | SV1 | Establecer Valor 1
Parametro 2: | XXXX | XXXX representa la longitud en HEXADECIMAL del string que se envía
con el valor del parámetro.
El valor viene como string detras del ultimo caracter del comando
Destino: | R00 | iROB-EA-00
Origen: | CTR | Sistema de Control
Funcion: | cmd_Comando_C_SRVY(&gd)

String a enviar

C_SRVY | Control Servo camara eje Y | #####100104100060001
Parametro 1: | INI | Inicializar
Parametro 2: | NOP | Nada
Destino: | R00 | iROB-EA-00
Origen: | CTR | Sistema de Control
Funcion: | cmd_Comando_C_SRVY(&gd)

String a enviar

C_STPC | Comando relacionados con el PC de control | #####1001070000E0001
Parametro 1: | ACT | Activar, Activado
Parametro 2: | NOP | Nada
Destino: | R00 | iROB-EA-00
Origen: | CTR | Sistema de Control
Funcion: | cmd_Comando_C_STPC(&gd)

String a enviar

C_STPC | Comando relacionados con el PC de control | #####1001070000F0001
Parametro 1: | DES | Desactivar, Desactivado
Parametro 2: | NOP | Nada
Destino: | R00 | iROB-EA-00
Origen: | CTR | Sistema de Control
Funcion: | cmd_Comando_C_STPC(&gd)

Gescom_MEGA2560_V3

String a enviar

CM_CTR | Comandos de control general | #####100100460000001
Parametro 1: | MD1 | Modo 1
Parametro 2: | NOP | Nada
Destino: | R00 | iROB-EA-00
Origen: | CTR | Sistema de Control
Funcion: | cmd_Comando_CM_CTR(&gd)

String a enviar

CM_CTR | Comandos de control general | #####100100460010001
Parametro 1: | MD2 | Modo 2
Parametro 2: | NOP | Nada
Destino: | R00 | iROB-EA-00
Origen: | CTR | Sistema de Control
Funcion: | cmd_Comando_CM_CTR(&gd)

String a enviar

CM_CTR | Comandos de control general | #####100100411010001
Parametro 1: | GV1 | Obtener Valor 1
Parametro 2: | NOP | Nada
Destino: | R00 | iROB-EA-00
Origen: | CTR | Sistema de Control
Funcion: | cmd_Comando_CM_CTR(&gd)

String a enviar

CM_DBG | Comandos DEBUG | #####1001002000E0001
Parametro 1: | ACT | Activar, Activado
Parametro 2: | NOP | Nada
Destino: | R00 | iROB-EA-00
Origen: | CTR | Sistema de Control
Funcion: | cmd_Comando_CM_DBG(&gd)

Gescom_MEGA2560_V3

String a enviar

CM_DBG | Comandos DEBUG | #####1001002000F0001
Parametro 1: | DES | Desactivar, Desactivado
Parametro 2: | NOP | Nada
Destino: | R00 | iROB-EA-00
Origen: | CTR | Sistema de Control
Funcion: | cmd_Comando_CM_DBG(&gd)

String a enviar

CM_DBG | Comandos DEBUG | #####100100211010001
Parametro 1: | GV1 | Obtener Valor 1
Parametro 2: | NOP | Nada
Destino: | R00 | iROB-EA-00
Origen: | CTR | Sistema de Control
Funcion: | cmd_Comando_CM_DBG(&gd)

String a enviar

CM_RTC | Comandos para el RTC de Arduino | #####10010031001XXXX
Parametro 1: | SV1 | Establecer Valor 1
Parametro 2: | XXXX | XXXX representa la longitud en HEXADECIMAL del string que se envía
con el valor del parámetro.
El valor viene como string detras del ultimo caracter del comando
Destino: | R00 | iROB-EA-00
Origen: | CTR | Sistema de Control
Funcion: | cmd_Comando_CM_RTC(&gd)

String a enviar

CM_RTC | Comandos para el RTC de Arduino | #####100100311010001
Parametro 1: | GV1 | Obtener Valor 1
Parametro 2: | NOP | Nada
Destino: | R00 | iROB-EA-00
Origen: | CTR | Sistema de Control
Funcion: | cmd_Comando_CM_RTC(&gd)

Gescom_MEGA2560_V3

String a enviar

S_9DOF | Sensores gestionados por 9DOF Razor IMU | #####100107111010001
Parametro 1: | GV1 | Obtener Valor 1
Parametro 2: | NOP | Nada
Destino: | R00 | iROB-EA-00
Origen: | CTR | Sistema de Control
Funcion: | cmd_Comando_S_9DOF(&gd)

String a enviar

S_9DOF | Sensores gestionados por 9DOF Razor IMU | #####100107111020001
Parametro 1: | GV2 | Obtener Valor 2
Parametro 2: | NOP | Nada
Destino: | R00 | iROB-EA-00
Origen: | CTR | Sistema de Control
Funcion: | cmd_Comando_S_9DOF(&gd)

String a enviar

S_9DOF | Sensores gestionados por 9DOF Razor IMU | #####100107111030001
Parametro 1: | GV3 | Obtener Valor 3
Parametro 2: | NOP | Nada
Destino: | R00 | iROB-EA-00
Origen: | CTR | Sistema de Control
Funcion: | cmd_Comando_S_9DOF(&gd)

String a enviar

S_9DOF | Sensores gestionados por 9DOF Razor IMU | #####100107111040001
Parametro 1: | GV4 | Obtener Valor 4
Parametro 2: | NOP | Nada
Destino: | R00 | iROB-EA-00
Origen: | CTR | Sistema de Control
Funcion: | cmd_Comando_S_9DOF(&gd)

Gescom_MEGA2560_V3

String a enviar

S_CFAN | Sensores, control del ventilador | #####100105700040001
Parametro 1: | OFF | Apagar
Parametro 2: | NOP | Nada
Destino: | R00 | iROB-EA-00
Origen: | CTR | Sistema de Control
Funcion: | cmd_Comando_S_CFAN(&gd)

String a enviar

S_CFAN | Sensores, control del ventilador | #####100105700050001
Parametro 1: | _ON | Encender
Parametro 2: | NOP | Nada
Destino: | R00 | iROB-EA-00
Origen: | CTR | Sistema de Control
Funcion: | cmd_Comando_S_CFAN(&gd)

String a enviar

S_GLUZ | Sensores de luz | #####100105211010001
Parametro 1: | GV1 | Obtener Valor 1
Parametro 2: | NOP | Nada
Destino: | R00 | iROB-EA-00
Origen: | CTR | Sistema de Control
Funcion: | cmd_Comando_S_GLUZ(&gd)

String a enviar

S_HUMR | Sensores de humedad | #####100105111010001
Parametro 1: | GV1 | Obtener Valor 1
Parametro 2: | NOP | Nada
Destino: | R00 | iROB-EA-00
Origen: | CTR | Sistema de Control
Funcion: | cmd_Comando_S_HUMR(&gd)

Gescom_MEGA2560_V3

String a enviar

S_PRES | Sensores Presion | #####100105911013000
Parametro 1: | GV1 | Obtener Valor 1
Parametro 2: | SSA | Subsensor A
Destino: | R00 | iROB-EA-00
Origen: | CTR | Sistema de Control
Funcion: | cmd_Comando_S_PRES(&gd)

String a enviar

S_PRES | Sensores Presion | #####100105911013001
Parametro 1: | GV1 | Obtener Valor 1
Parametro 2: | SSB | Subsensor B
Destino: | R00 | iROB-EA-00
Origen: | CTR | Sistema de Control
Funcion: | cmd_Comando_S_PRES(&gd)

String a enviar

S_RGPS | Sensor GPS | #####100105400100001
Parametro 1: | RFS | Actualizar, refrescar
Parametro 2: | NOP | Nada
Destino: | R00 | iROB-EA-00
Origen: | CTR | Sistema de Control
Funcion: | cmd_Comando_S_RGPS(&gd)

String a enviar

S_RGPS | Sensor GPS | #####100105411010001
Parametro 1: | GV1 | Obtener Valor 1
Parametro 2: | NOP | Nada
Destino: | R00 | iROB-EA-00
Origen: | CTR | Sistema de Control
Funcion: | cmd_Comando_S_RGPS(&gd)

Gescom_MEGA2560_V3

String a enviar

S_RGPS | Sensor GPS | #####100105411020001
Parametro 1: | GV2 | Obtener Valor 2
Parametro 2: | NOP | Nada
Destino: | R00 | iROB-EA-00
Origen: | CTR | Sistema de Control
Funcion: | cmd_Comando_S_RGPS(&gd)

String a enviar

S_RGPS | Sensor GPS | #####100105411030001
Parametro 1: | GV3 | Obtener Valor 3
Parametro 2: | NOP | Nada
Destino: | R00 | iROB-EA-00
Origen: | CTR | Sistema de Control
Funcion: | cmd_Comando_S_RGPS(&gd)

String a enviar

S_RGPS | Sensor GPS | #####100105411040001
Parametro 1: | GV4 | Obtener Valor 4
Parametro 2: | NOP | Nada
Destino: | R00 | iROB-EA-00
Origen: | CTR | Sistema de Control
Funcion: | cmd_Comando_S_RGPS(&gd)

String a enviar

S_RGPS | Sensor GPS | #####100105411050001
Parametro 1: | GV5 | Obtener Valor 5
Parametro 2: | NOP | Nada
Destino: | R00 | iROB-EA-00
Origen: | CTR | Sistema de Control
Funcion: | cmd_Comando_S_RGPS(&gd)

Gescom_MEGA2560_V3

String a enviar

S_RGPS | Sensor GPS | #####100105411060001
Parametro 1: | GV6 | Obtener Valor 6
Parametro 2: | NOP | Nada
Destino: | R00 | iROB-EA-00
Origen: | CTR | Sistema de Control
Funcion: | cmd_Comando_S_RGPS(&gd)

String a enviar

S_RGPS | Sensor GPS | #####100105411070001
Parametro 1: | GV7 | Obtener Valor 7
Parametro 2: | NOP | Nada
Destino: | R00 | iROB-EA-00
Origen: | CTR | Sistema de Control
Funcion: | cmd_Comando_S_RGPS(&gd)

String a enviar

S_SALT | Sensores de altitud | #####100105811010001
Parametro 1: | GV1 | Obtener Valor 1
Parametro 2: | NOP | Nada
Destino: | R00 | iROB-EA-00
Origen: | CTR | Sistema de Control
Funcion: | cmd_Comando_S_SALT(&gd)

String a enviar

S_SEUS | Sensores ultrasonidos | #####100105611013000
Parametro 1: | GV1 | Obtener Valor 1
Parametro 2: | SSA | Subsensor A
Destino: | R00 | iROB-EA-00
Origen: | CTR | Sistema de Control
Funcion: | cmd_Comando_S_SEUS(&gd)

Gescom_MEGA2560_V3

String a enviar

S_SEUS | Sensores ultrasonidos | #####100105611013001
Parametro 1: | GV1 | Obtener Valor 1
Parametro 2: | SSB | Subsensor B
Destino: | R00 | iROB-EA-00
Origen: | CTR | Sistema de Control
Funcion: | cmd_Comando_S_SEUS(&gd)

String a enviar

S_SICC | Sensores de corriente | #####1001055000D0001
Parametro 1: | CAL | Calibrar
Parametro 2: | NOP | Nada
Destino: | R00 | iROB-EA-00
Origen: | CTR | Sistema de Control
Funcion: | cmd_Comando_S_SICC(&gd)

String a enviar

S_SICC | Sensores de corriente | #####100105511013000
Parametro 1: | GV1 | Obtener Valor 1
Parametro 2: | SSA | Subsensor A
Destino: | R00 | iROB-EA-00
Origen: | CTR | Sistema de Control
Funcion: | cmd_Comando_S_SICC(&gd)

String a enviar

S_SICC | Sensores de corriente | #####100105511013001
Parametro 1: | GV1 | Obtener Valor 1
Parametro 2: | SSB | Subsensor B
Destino: | R00 | iROB-EA-00
Origen: | CTR | Sistema de Control
Funcion: | cmd_Comando_S_SICC(&gd)

Gescom_MEGA2560_V3

String a enviar

S_SSUP | Sensores superficie | #####100105311010001
Parametro 1: | GV1 | Obtener Valor 1
Parametro 2: | NOP | Nada
Destino: | R00 | iROB-EA-00
Origen: | CTR | Sistema de Control
Funcion: | cmd_Comando_S_SSUP(&gd)

String a enviar

S_TEMP | Sensores de temperatura | #####100105011013000
Parametro 1: | GV1 | Obtener Valor 1
Parametro 2: | SSA | Subsensor A
Destino: | R00 | iROB-EA-00
Origen: | CTR | Sistema de Control
Funcion: | cmd_Comando_S_TEMP(&gd)

String a enviar

S_TEMP | Sensores de temperatura | #####100105011013001
Parametro 1: | GV1 | Obtener Valor 1
Parametro 2: | SSB | Subsensor B
Destino: | R00 | iROB-EA-00
Origen: | CTR | Sistema de Control
Funcion: | cmd_Comando_S_TEMP(&gd)

String a enviar

S_TEMP | Sensores de temperatura | #####100105011013002
Parametro 1: | GV1 | Obtener Valor 1
Parametro 2: | SSC | Subsensor C
Destino: | R00 | iROB-EA-00
Origen: | CTR | Sistema de Control
Funcion: | cmd_Comando_S_TEMP(&gd)

Gescom_MEGA2560_V3

String a enviar

S_TEMP | Sensores de temperatura | #####100105011013003
Parametro 1: | GV1 | Obtener Valor 1
Parametro 2: | SSD | Subsensor D
Destino: | R00 | iROB-EA-00
Origen: | CTR | Sistema de Control
Funcion: | cmd_Comando_S_TEMP(&gd)

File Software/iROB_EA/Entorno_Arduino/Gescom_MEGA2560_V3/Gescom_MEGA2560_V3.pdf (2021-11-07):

# GESCOM_MEGA2560

V3

# GESTOR DE COMANDOS

VERSIÓN PARA ARDUINO MEGA 2560

Fecha Doc.: 01 de marzo de 2016
Versión: | 3.00

GESCOM_MEGA2560, GESTOR DE COMANDOS, V3

# 1 TABLA DE CONTENIDO

# 2 LIBRERÍA GESCOM_MEGA2560

La librería GESCOM (Gestor de Comandos), versión 3.0 implementa un gestor de comandos de propósito general que permite enviar comandos entre dispositivos (Robots, PCs etc).
Esta librería se ha creado con el objeto de que sea independiente de la implementación física de las operaciones que ejecute cada comando, de forma que el gestor se pueda utilizar en cualquier Dispositivo.

Esta versión está adpatada para que se pueda utilizar con la placa Arduino MEGA2560 porque permite la utilización de cualquier puerto serie.

# 2.1 ABREVIATURAS Y DEFINICIONES

- GC, Gestor de comandos.
Es el gestor de comandos descrito en este documento.

# 2.2 DOCUMENTOS RELACIONADOS

Documentos relacionados con Gescom_MEGA2560

- Gescom_MEGA2560_V3.mdb
Base de Datos Access para creación y gestión de comandos.
Esta | BBDD | permite | también | la | obtención | de | los | dos | ficheros
(Gescom_MEGA2560_V3_CMD.h y Gescom_MEGA2560_V3_FProceso.cpp) que implementan los comandos definidos en la BBDD y que deben ser incluidos en la librería Gescom del directorio de librerías del IDE de Arduino cada vez que se actualiza/crean comandos.
- Instrucciones_BBDD.doc
Documento | word | con | instrucciones | de | uso | de | la | BBDD
Gescom_MEGA2560_V3.mdb
- Instrucciones_Libreria.doc
Documento Word para creación de la librería Gescom_MEGA2560 que se debe copiar en el directorio de librerías del IDE de Arduino.

# 3 COMANDOS

GC se comunica mediante comandos que se envian por un puerto serie.
Después de la ejecución de un comando, GC envía una respuesta, si se produce algún error en la transmisión de los caracteres la función que implentan el gestor exeGesComando() retornará un error.

Un comando es una secuencia de caracteres ASCII que al ser recibidos se procesan y dan como resultado la llamada a una cierta función.

Para mantener activo el GC es necesario llamar a la función exeGesComando() por lo que un buen lugar para colocar la llamada a esta función es la función loop() de los programas de Arduino.

01/06/2015

# 3.1 DEFINICIÓN DE COMANDO

Seguidamente se muestra la sintáxis de un comando (comando de envío) y la respuesta que se recibe desde el GC después de su ejecución (comando respuesta), es importante destacar que después de la ejcución de un comando, el GC siempre genera un comando de respuesta.
Los comandos son secuencias de caractéres ASCII de longitud fija (20 caractéres), salvo para comandos que envíen datos adicionales.

# 3.1.1 COMANDOS DE ENVÍO

Los comandos que se envían desde el sistema de control al dispositivo para su ejecución tienen la siguiente estructura,

X | X | X | X | X | D | D | O | O | T | C | C | P1 | P1 | P1 | P1 | P2 | P2 | P2 | P2 | …
CABECERA | DESTINO | ORIGEN | TIPO | COMANDO ID | PARÁMETRO 1 | PARAMETRO 2 | Segundo parámetro
| | | | | | | Primer parámetro
| | | | | | | ID Comando
| | | | | | | Tipo de comando ( envio/respuesta)
| | | | | | | Origen del comando
| | | | | | | Destino del comando
| | | | | | | Cabecera que indica comienzo del comando

# 3.1.2 COMANDOS DE RESPUESTA

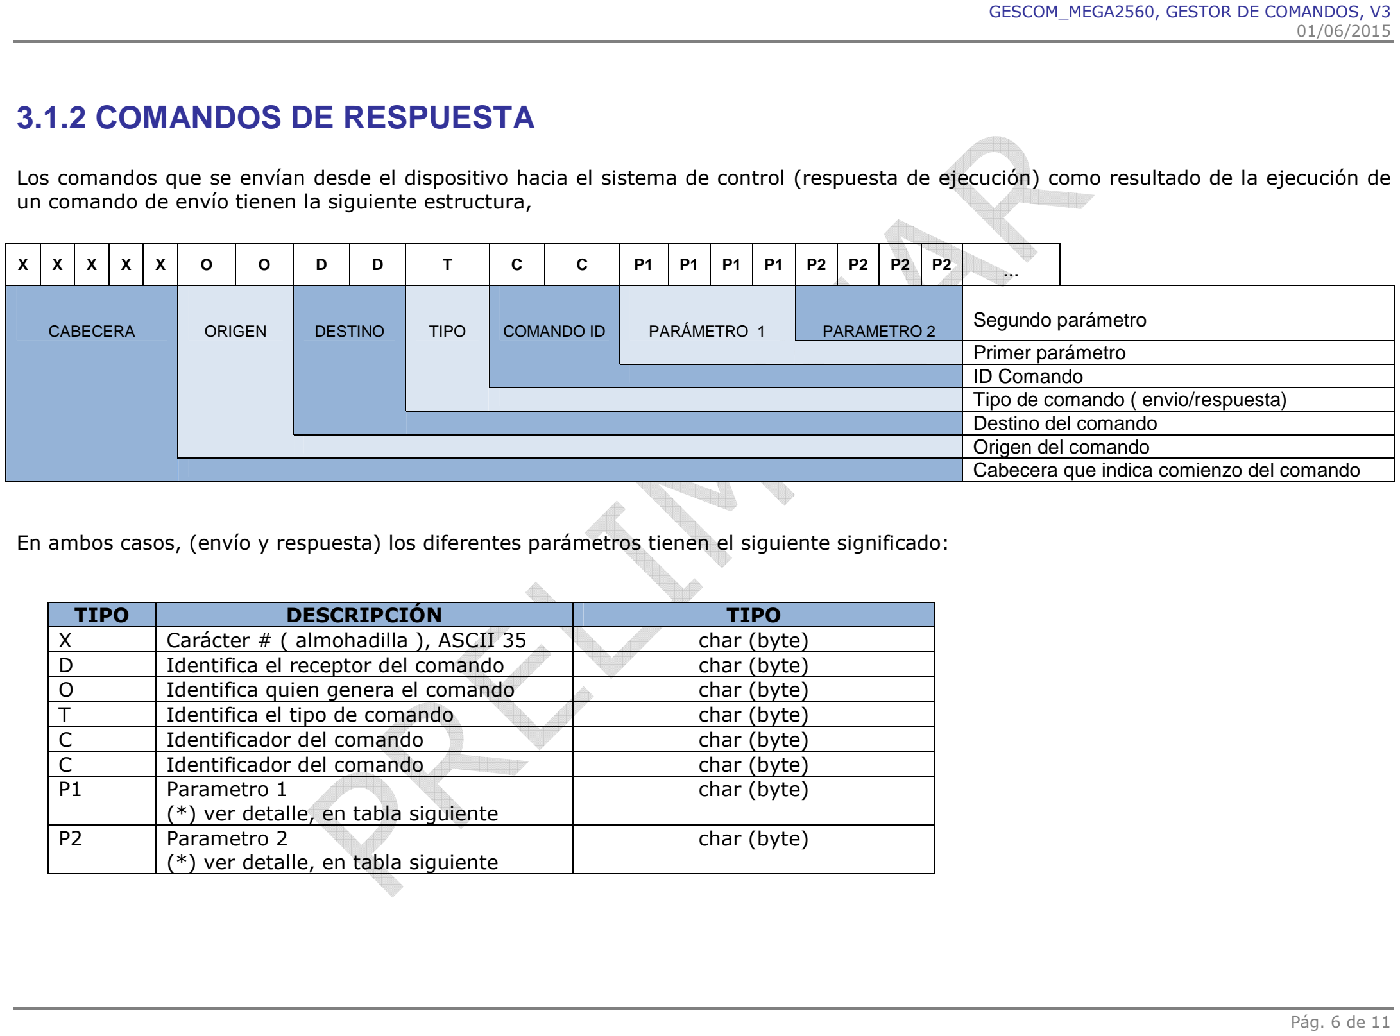
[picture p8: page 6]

01/06/2015

Los comandos que se envían desde el dispositivo hacia el sistema de control (respuesta de ejecución) como resultado de la ejecución de un comando de envío tienen la siguiente estructura,

En ambos casos, (envío y respuesta) los diferentes parámetros tienen el siguiente significado:

TIPO | DESCRIPCIÓN | TIPO
X | Carácter # ( almohadilla ), ASCII 35 | char (byte)
D | Identifica el receptor del comando | char (byte)
O | Identifica quien genera el comando | char (byte)
T | Identifica el tipo de comando | char (byte)
C | Identificador del comando | char (byte)
C | Identificador del comando | char (byte)
P1 | Parametro 1 (*) ver detalle, en tabla siguiente | char (byte)
P2 | Parametro 2 (*) ver detalle, en tabla siguiente | char (byte)
X | X | X | X | X | O | O | D | D | T | C | C | P1 | P1 | P1 | P1 | P2 | P2 | P2 | P2 | …
CABECERA | ORIGEN | DESTINO | TIPO | COMANDO ID | PARÁMETRO 1 | PARAMETRO 2 | Segundo parámetro
| | | | | | | Primer parámetro
| | | | | | | ID Comando
| | | | | | | Tipo de comando ( envio/respuesta)
| | | | | | | Destino del comando
| | | | | | | Origen del comando
| | | | | | | Cabecera que indica comienzo del comando

- X, cabecera

### 5 caracteres que indican el comienzo de un comando, son siempre caractéres #

(almohadilla), ASCII 35.

- D, destino

### 2 caracteres que indican en hexadecimal el dispositivo destino al que se dirije el

comando.

- O, origen
2 caracteres que indican en hexadecimal el dispositivo origen que envía el comando.

Nota:
(ver la tabla “Tbl_Dispositivos” en gescom_MEGA2560_V3.mdb)
- T, Tipo

### 1 caracter que indica:

0 Comando de envío
1 Comando de respuesta
- C, comando ID
2 caracteres que identifican en hexadecimal el comando.

Nota:
(ver la tabla “Tbl_Comandos” en gescom_MEGA2560_V3.mdb)
- CARÁCTER P1, parámetro 1.
4 carcteres que identifican en hexdecimal el parámetro 1.

Importante:
Si es un comando de envío: valor
Si es un comando de respuesta: 0

Nota:
(ver la tabla “Tbl_Parametros” en gescom_MEGA2560_V3.mdb)

- CARÁCTER P2, parámetro 2.
4 carcteres que identifican en hexdecimal el parámetro 2.

Importante:
Si es un comando de envío: | valor
Si es un comando de respuesta: 0 | Si el comando no genera datos de respuesta
Valor longitud en bytes del string que retorna
el comando como respuesta.
La longitud MÁXIMA que se puede retornar es de IDE_MAXL_RESP_CMD ( actualmente fijado en 25 bytes), este define se encuentra en Gescom_MEGA2560_V3.h

Nota:
(ver la tabla “Tbl_Parametros” en gescom_MEGA2560_V3.mdb)

El mecanismo de funcionamiento es el siguiente:

- El comando se envía o recibe utilizando la comunicación serie, através del puerto indicado en el constructor del objeto,

#define IDE_SERIAL_0

#define IDE_SERIAL_1

#define IDE_SERIAL_2

#define IDE_SERIAL_3

- El Gestor de comandos recibe el comando, comprueba su sintáxis y una vez determinado que es un comando válido llama a una determinada función de usuario para procesarlo.

En la carpeta de “Gescom_MEGA2560_V3\examples”, existe un fichero .ino con una función de interfaz creada vacia.

Los comandos y parámetros soportados por esta versión se gestionan desde la base de datos Gescom_MEGA2560_V3.mdb.

# 3.1.3 CREACIÓN, MODIFICACIÓN COMANDOS

Para crear, modificar y eliminar comandos se debe utilizar la base de datos Access Gescom_MEGA2560_V3.mdb.
Para más información sobre la utilización de esta BBDD ver el documento Instrucciones_BBDD.doc

# 3.2 CAMBIOS

La definición de la estrcutura de comandos de esta versión es incompatible con las anateriores versiones de la librería.

# 3.3 UTILIZACIÓN DE LA LIBRERÍA GESCOM

La forma típica de utilización de esta librería será:

#include <Gescom_MEGA2560_V3.h>

### #include<Gescom_MEGA2560_V3_CMD.h>

GESCOM3 gc = GESCOM3(puertoID,modo,dispositivoID,velocidad); // ---------------------------------------------------------// . puertoID:
// | puede ser cualquiera de los defines (incluidos en el
// | define “Gescom_MEGA2560_V3.h”)que identifican los
// | puertos serie del Arduino MEGA2560
//
// | IDE_SERIAL_0
// | IDE_SERIAL_1
// | IDE_SERIAL_2
// | IDE_SERIAL_3
//
// . modo:
// | true Modo DEBUG
// | false Modo real
//
// . dispositivoID:
// Valor en hexadecimal que identifica el Robot (0x00 … 0xFF) //
// . Velocidad
// Velocidad del puerto (tipicamente 9600)
//
// ---------------------------------------------------------

// ---------------------------------------------------------//
// void setup()
// | Funcion setup de proyectos Arduino
//
// ---------------------------------------------------------

void setup()
{
}

// ---------------------------------------------------------//
// void loop()
// | Funcion setup de proyectos Arduino
//
// ---------------------------------------------------------

void loop()
{
| gc.exeGesComando();
}

Para más información, ver el ejemplo gescom_demo.ino del directorio examples de la librería.

# 3.3.1 INSTALACIÓN

Para | poder | utilizar | la | librería | es | necesario | copiar | la | carpeta
“gescom_MEGA2560_V3” en el directorio de librerias de la versión del IDE de Arduino que se esté utilizado, por ejemplo para la versión arduino-1.0.4,

arduino-1.0.4\libraries\Gescom_MEGA2560_V3

# 3.3.2 DESCRIPCIÓN DE LA CLASE GESCOM

Todos los defines relacionados con el gestor de comandos se encuentran en el include gescom_MEGA2560_V3_CMD.h.

En la actual versión, la clase GESCOM3 tiene tres miembros públicos:

void GESCOM3::gescom( int puertoID,
int debug,
byte robID,
long int velocidad
);

Inicializa la clase y abre el puerto serie indicado por el parámetro “puertoID”, inicializándolo a la velocidad indicada en “velocidad”, se recomienda 9600.

- puertoID puede ser:

IDE_SERIAL_0 Identifica el puerto serie 0
IDE_SERIAL_1 Identifica el puerto serie 1 IDE_SERIAL_2 Identifica el puerto serie 2 IDE_SERIAL_3 Identifica el puerto serie 3

Si se introduce un valor no válido se seleccionará el puerto 0

- debug puede ser:

true | Habilitar depuración.
false | Deshabilitar depuración.
- robID puede ser:
1 valor (0x00…0xFF) que identifica el Robot.
Gescom solo procesará comandos cuyo “robID” sea el especificado en este parámetro.
- Velocidad:
Velocidad del transmisión (9600, etc).

int GESCOM::exeGesComando(void);

Ejecuta el gestor de comandos.
Retorna:
- IDE_BUFF_RX_OK | Se ha recibido algo valido.
En este caso el comando se habrá ejecutado

NOTA:
Al recibir un comando siempre se comprueba el ID que identifica el dispositivo al que se dirige ese comando.
Si el ID del comando NO es el de este dispositivo, el comando se ignora y no se ejecuta.
- IDE_BUFF_RX_ER | Se ha recibido algo erroneo.
No se ha ejecutado nada
- IDE_BUFF_RX_VACIO | NO se ha recibido nada o si el ROB ID del
comando | recibido | no | corresponde | con | el
indicado en el constructor de la clase.
En este caso se retorna inmediatamente al programa principal.

int GESCOM3::getBytes(char* buff, int nBytes);

Lee del puerto serie asociado a la clase, el número de bytes indicados en el parámetro nBytes y los almacena en el buffer que recibe en el parámetro “buff”, que debe contener espacio para los mismos.
Retorna el número de caracteres leidos, si todo ha ido correcto coincidirá con el número de bytes requeridos en el parámetro nBytes.
Si se produce error o no hay caracteres retorna 0.

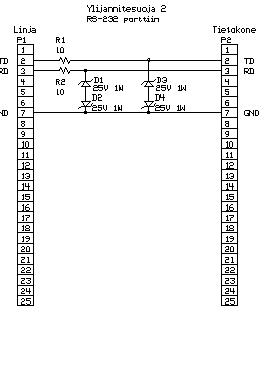
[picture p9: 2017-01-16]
Hardware/V1.0.0/Proteccion_RS232.jpg

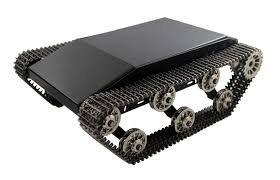
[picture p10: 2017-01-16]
Doc/Documentacion/Ilustraciones/trex-01.png

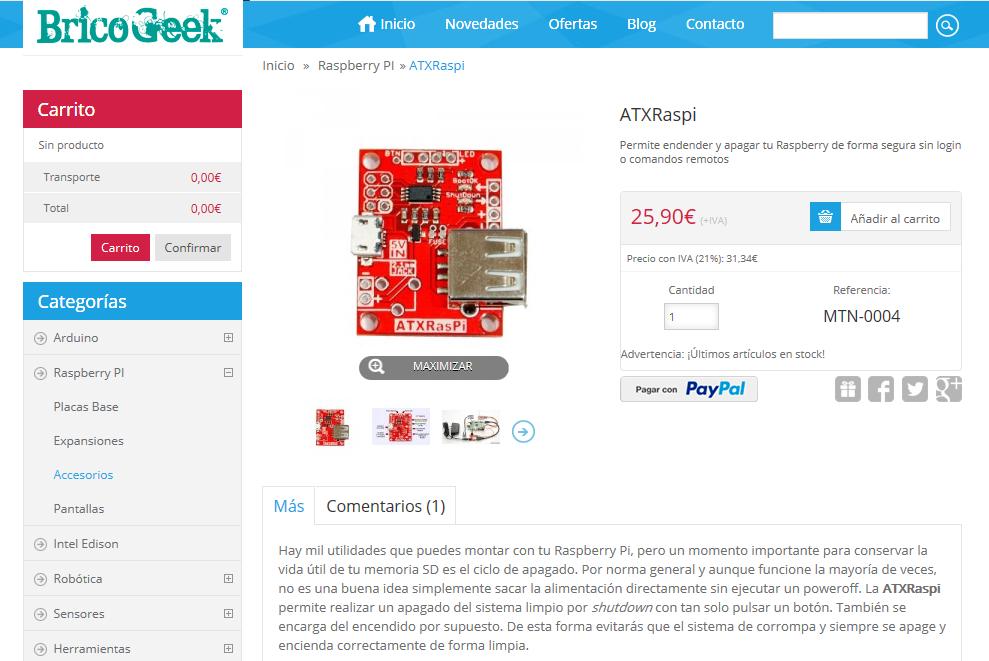
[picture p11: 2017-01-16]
Doc/DataSheet/OLDS/Raspberry_ATXRaspi/Raspberry_Encendido_Apagado.jpg

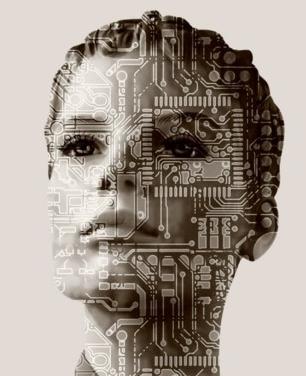
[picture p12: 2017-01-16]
Doc/Documentacion/digital.jpg

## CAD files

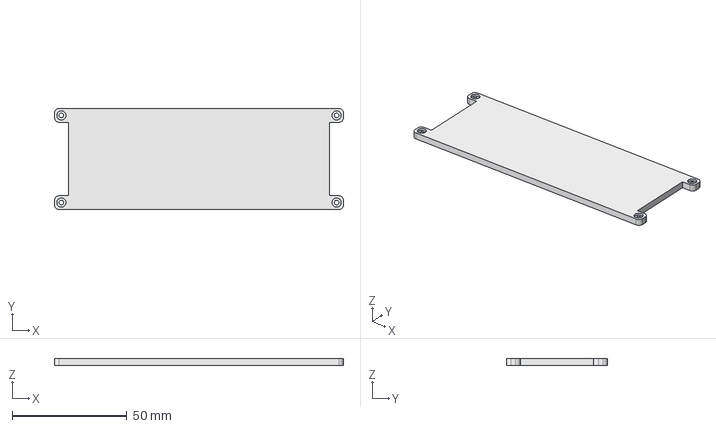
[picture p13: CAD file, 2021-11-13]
Hardware/V1.0.0/Ficheros_CAD_Impresora_3D/iROB-EA_ModuloPrincipal_Lateral_USB_Tapa.FCStd
126.0 x 44.0 x 3.00 mm

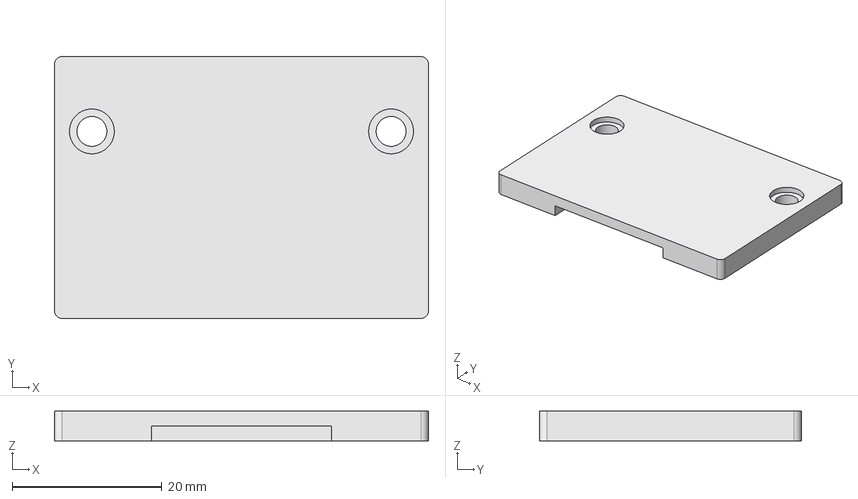
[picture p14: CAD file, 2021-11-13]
Hardware/V1.0.0/Ficheros_CAD_Impresora_3D/iROB-EA_ModuloPrincipal_Protector_Cables.FCStd
50.0 x 35.0 x 4.00 mm

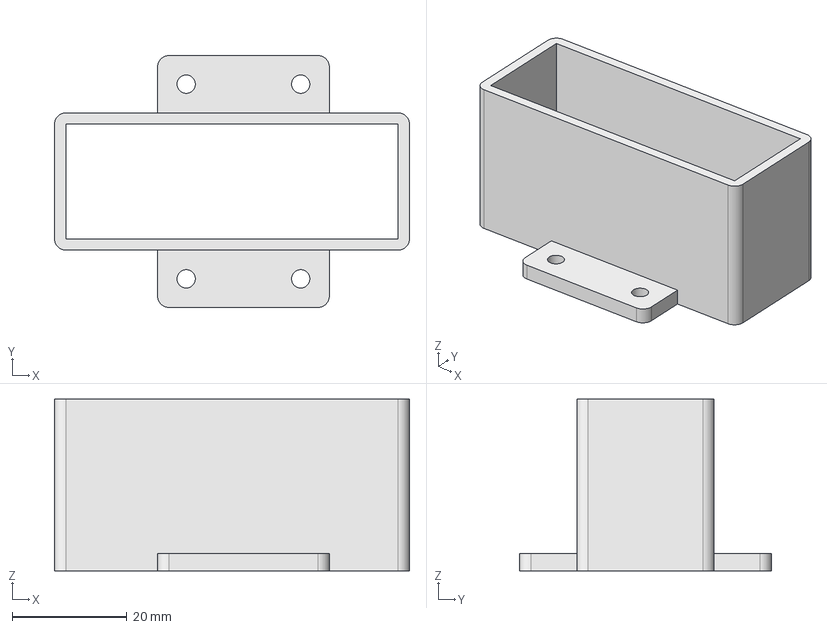
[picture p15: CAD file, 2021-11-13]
Hardware/V1.0.0/Ficheros_CAD_Impresora_3D/iROB-EA_Camara_Soporte_Servo.FCStd
62.0 x 44.0 x 30.0 mm

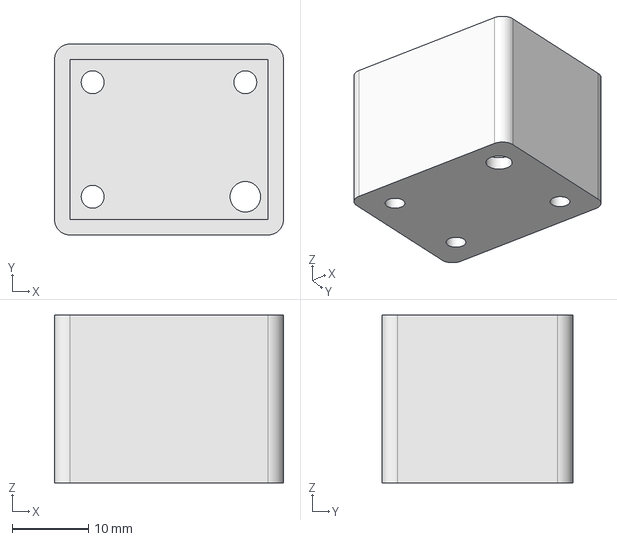
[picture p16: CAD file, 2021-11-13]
Hardware/V1.0.0/Ficheros_CAD_Impresora_3D/iROB-EA_Camara_Microfono.FCStd
30.0 x 25.0 x 22.0 mm

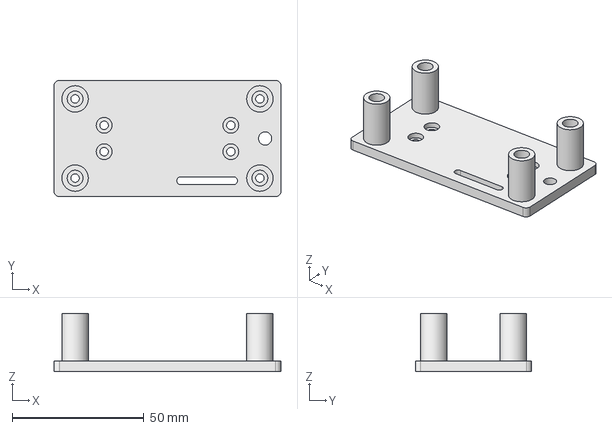
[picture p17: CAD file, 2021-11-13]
Hardware/V1.0.0/Ficheros_CAD_Impresora_3D/iROB-EA_Camara_Soporte_Robot.FCStd
86.0 x 44.0 x 22.0 mm

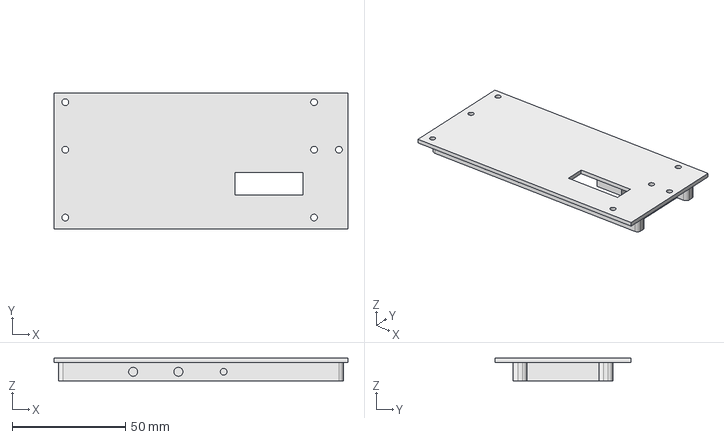
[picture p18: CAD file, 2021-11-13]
Hardware/V1.0.0/Ficheros_CAD_Impresora_3D/iROB-EA_ModuloPrincipal_Lateral_USB.FCStd
130.0 x 60.0 x 10.0 mm

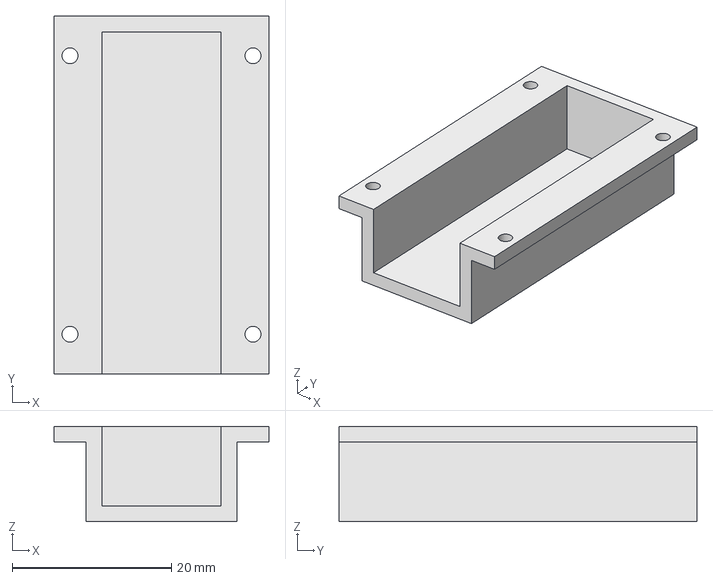
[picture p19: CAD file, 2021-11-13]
Hardware/V1.0.0/Ficheros_CAD_Impresora_3D/iROB-EA_Camara_Salida_Cables.FCStd
27.0 x 45.0 x 12.0 mm

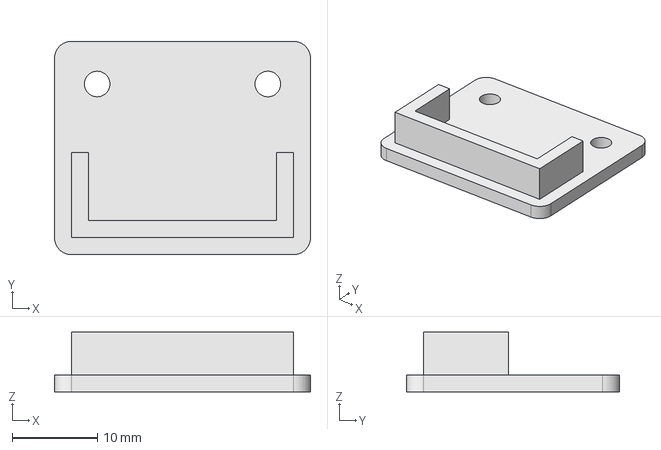
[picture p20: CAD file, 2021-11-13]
Hardware/V1.0.0/Ficheros_CAD_Impresora_3D/iROB-EA_Camara_Microfono_Tapa.FCStd
30.0 x 25.0 x 7.00 mm

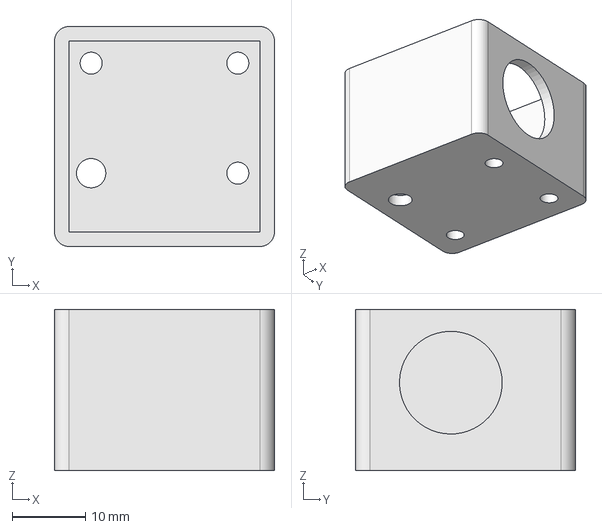
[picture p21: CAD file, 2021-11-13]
Hardware/V1.0.0/Ficheros_CAD_Impresora_3D/iROB-EA_Camara_Foco.FCStd
30.0 x 30.0 x 22.0 mm

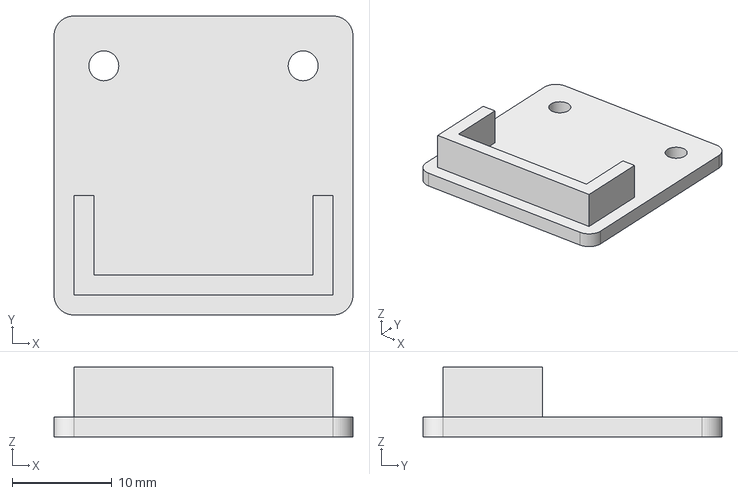
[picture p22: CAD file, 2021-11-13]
Hardware/V1.0.0/Ficheros_CAD_Impresora_3D/iROB-EA_Camara_Foco_Tapa.FCStd
30.0 x 30.0 x 7.00 mm

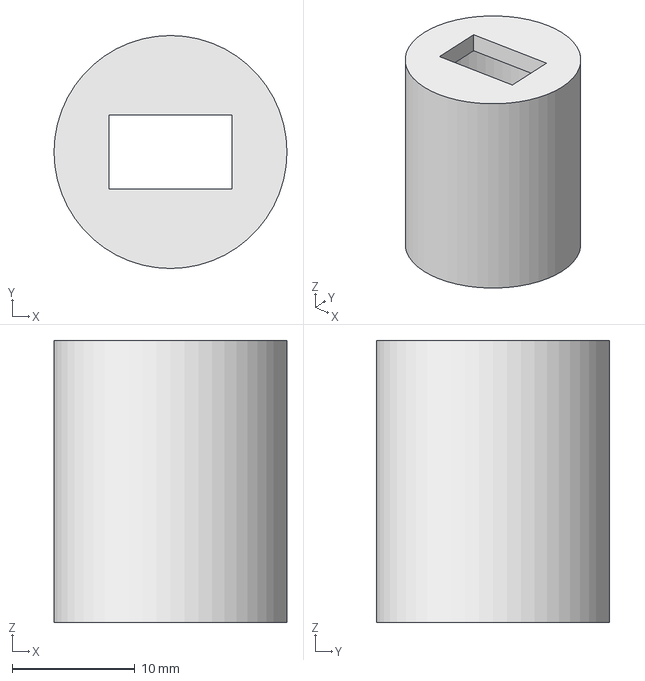
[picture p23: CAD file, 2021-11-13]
Hardware/V1.0.0/Ficheros_CAD_Impresora_3D/iROB-EA_Camara_Foco_Cilindro.FCStd
19.0 x 19.0 x 23.0 mm

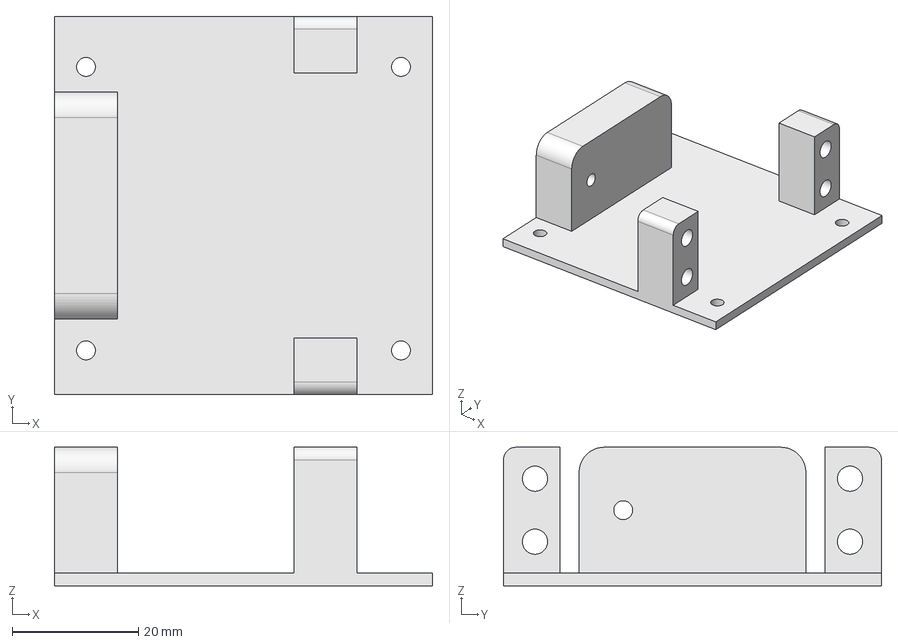
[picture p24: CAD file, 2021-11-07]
Hardware/V1.0.0/Ficheros_CAD_Impresora_3D/iROB-EA_Camara_Servo_Y.FCStd
60.0 x 60.0 x 22.0 mm

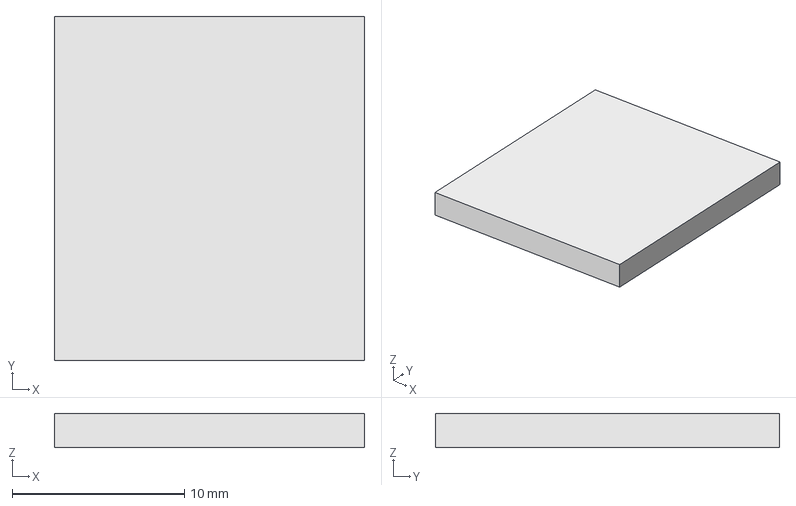
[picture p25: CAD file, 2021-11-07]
Hardware/V1.0.0/Ficheros_CAD_Impresora_3D/iROB-EA_Modulo_Sensores_Tapa_Cable_Servo.FCStd
18.0 x 20.0 x 2.00 mm

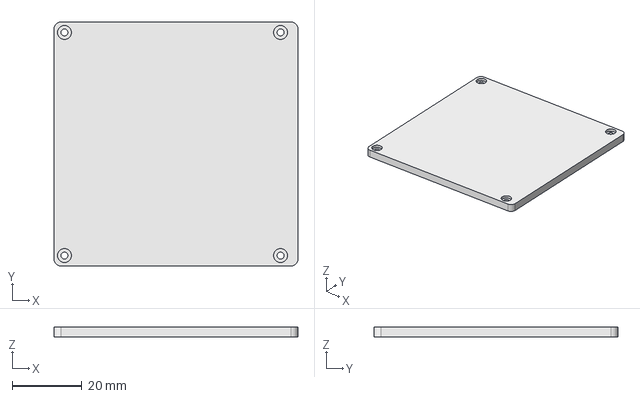
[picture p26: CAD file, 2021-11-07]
Hardware/V1.0.0/Ficheros_CAD_Impresora_3D/iROB-EA_Camara_Tapa.FCStd
70.0 x 70.0 x 3.00 mm

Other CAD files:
Hardware/V1.0.0/Ficheros_CAD_Impresora_3D/iROB-EA_Caja_Adaptador_Tapa_DEBUG.FCStd
Hardware/V1.0.0/Ficheros_CAD_Impresora_3D/iROB-EA_Tapa_RTC.FCStd
Hardware/V1.0.0/Ficheros_CAD_Impresora_3D/iROB-EA_Camara_Servo_Sujeccion_X.FCStd
Hardware/V1.0.0/Ficheros_CAD_Impresora_3D/iROB-EA_ModuloPrincipal.FCStd
Hardware/V1.0.0/Ficheros_CAD_Impresora_3D/iROB-EA_Caja_Adaptador_DEBUG.FCStd
Hardware/V1.0.0/Ficheros_CAD_Impresora_3D/iROB-EA_Caja_Adaptador_DEBUG.stl
Hardware/V1.0.0/Ficheros_CAD_Impresora_3D/iROB-EA_Caja_Adaptador_Tapa_DEBUG.stl
Hardware/V1.0.0/Ficheros_CAD_Impresora_3D/iROB-EA_Caja_RTC.FCStd
Hardware/V1.0.0/Ficheros_CAD_Impresora_3D/iROB-EA_Caja_RTC.stl
Hardware/V1.0.0/Ficheros_CAD_Impresora_3D/iROB-EA_Camara.FCStd
Hardware/V1.0.0/Ficheros_CAD_Impresora_3D/iROB-EA_Camara.stl
Hardware/V1.0.0/Ficheros_CAD_Impresora_3D/iROB-EA_Camara_Foco.stl
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

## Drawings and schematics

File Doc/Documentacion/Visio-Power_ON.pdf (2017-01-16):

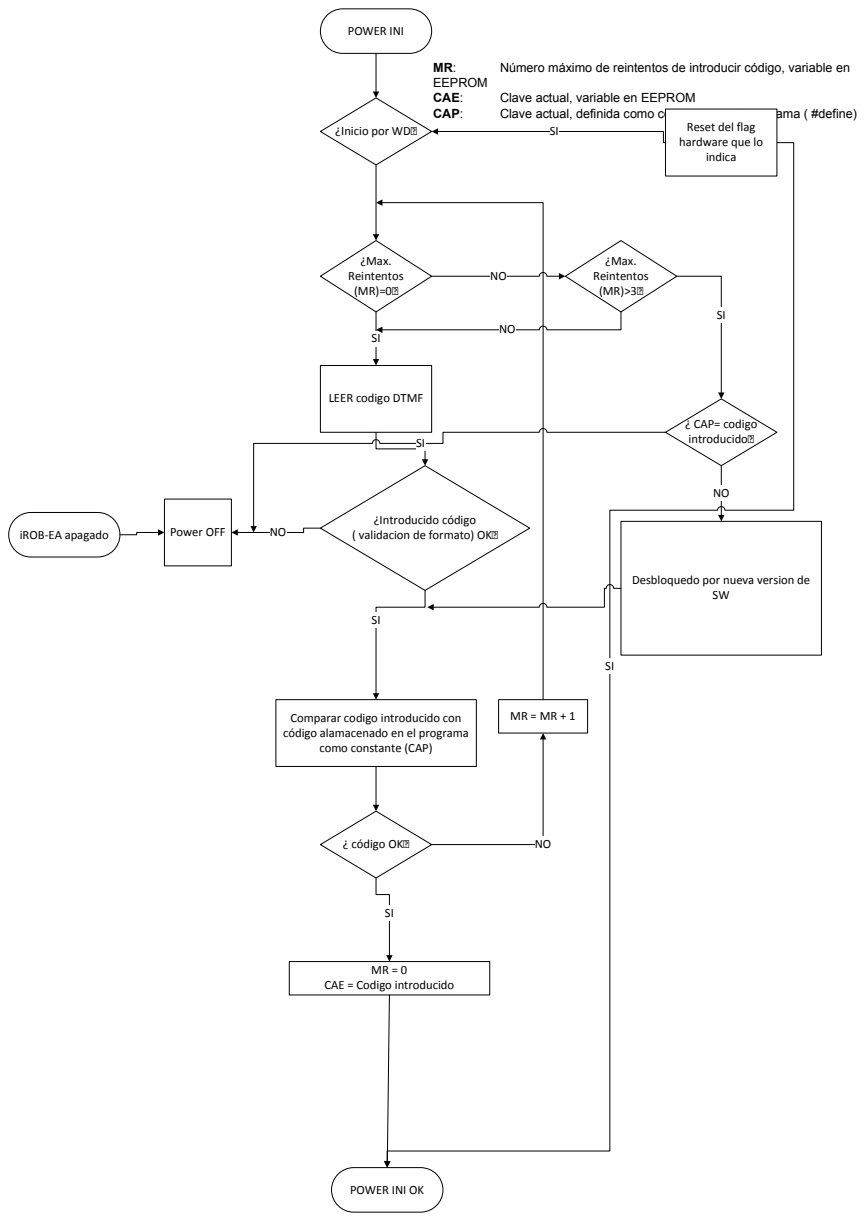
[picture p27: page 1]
POWER INI; ¿Max. Reintentos (MR)=0?; ¿Introducido código; iROB-EA apagado; Power OFF; ( validacion de formato) OK?; Número máximo de reintentos de introducir código, variable en; EEPROM; CAE:; Clave actual, variable en EEPROM; CAP:; Clave actual, definida como constante en el programa ( #define); ¿ código OK?; ¿Max. Reintentos (MR)>3?; ¿ CAP= codigo introducido? SI

¿Inicio por WD?

Reset del flag
hardware que lo
indica

LEER codigo DTMF

Desbloquedo por nueva version de

Comparar codigo introducido con
código alamacenado en el programa

como constante (CAP)

CAE = Codigo introducido

POWER INI OK

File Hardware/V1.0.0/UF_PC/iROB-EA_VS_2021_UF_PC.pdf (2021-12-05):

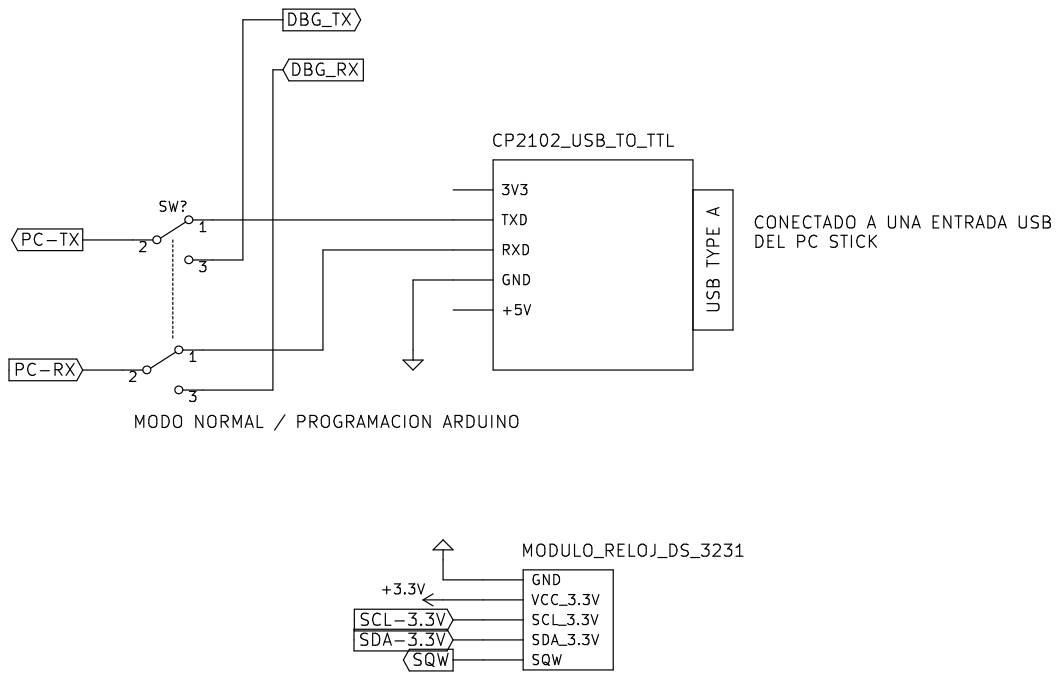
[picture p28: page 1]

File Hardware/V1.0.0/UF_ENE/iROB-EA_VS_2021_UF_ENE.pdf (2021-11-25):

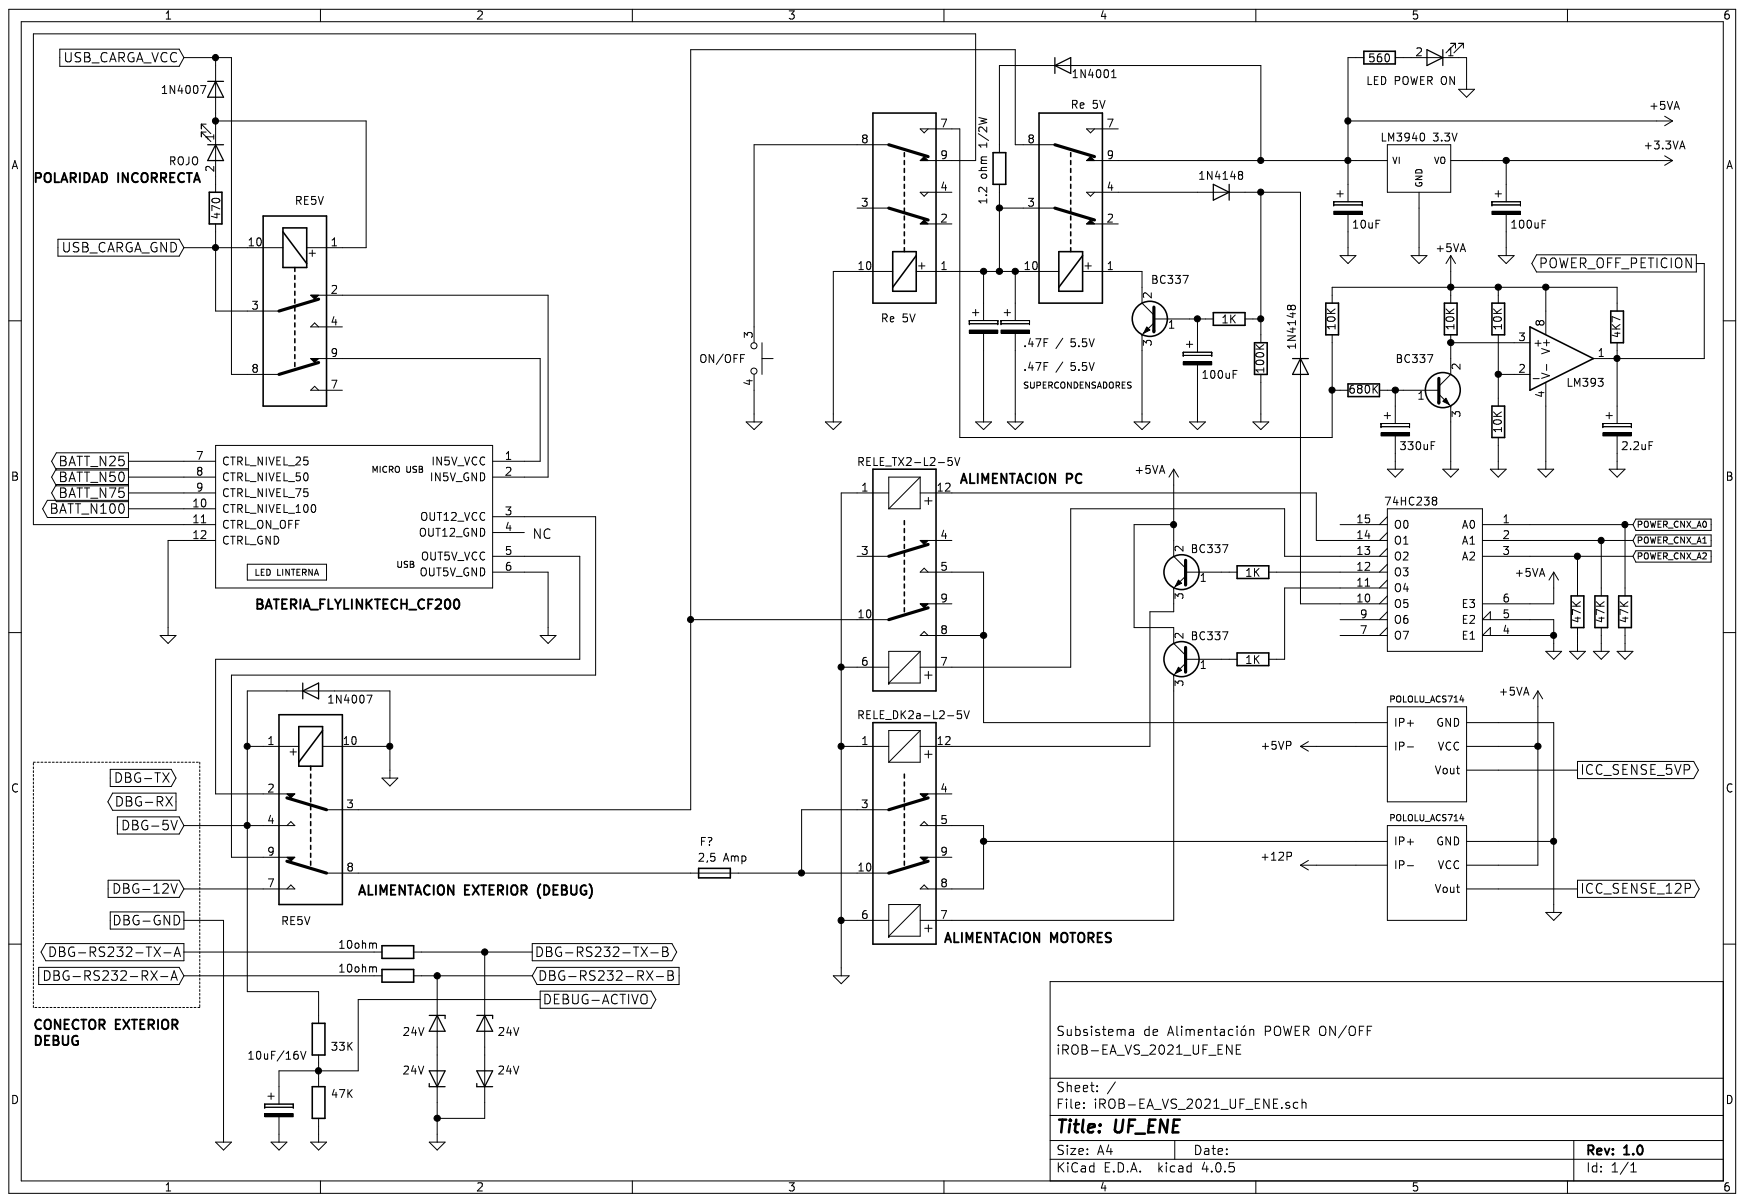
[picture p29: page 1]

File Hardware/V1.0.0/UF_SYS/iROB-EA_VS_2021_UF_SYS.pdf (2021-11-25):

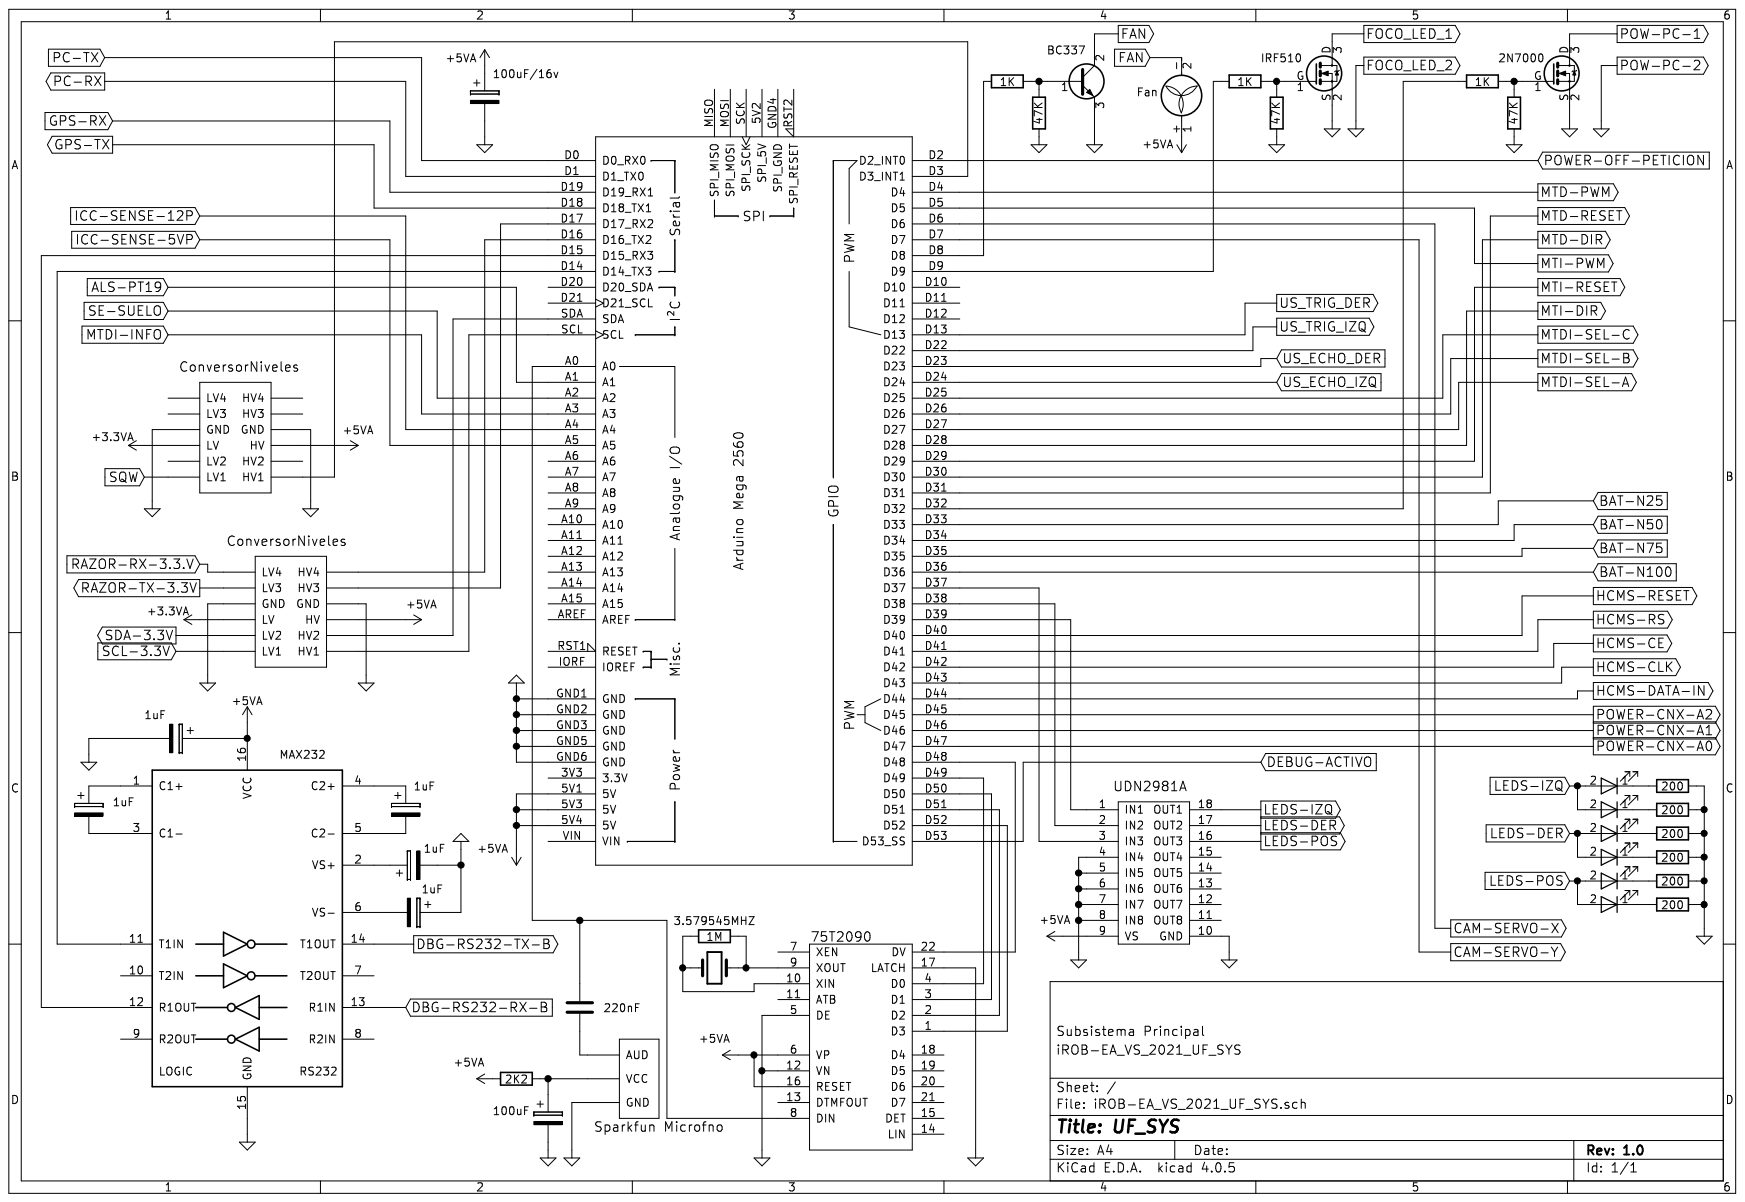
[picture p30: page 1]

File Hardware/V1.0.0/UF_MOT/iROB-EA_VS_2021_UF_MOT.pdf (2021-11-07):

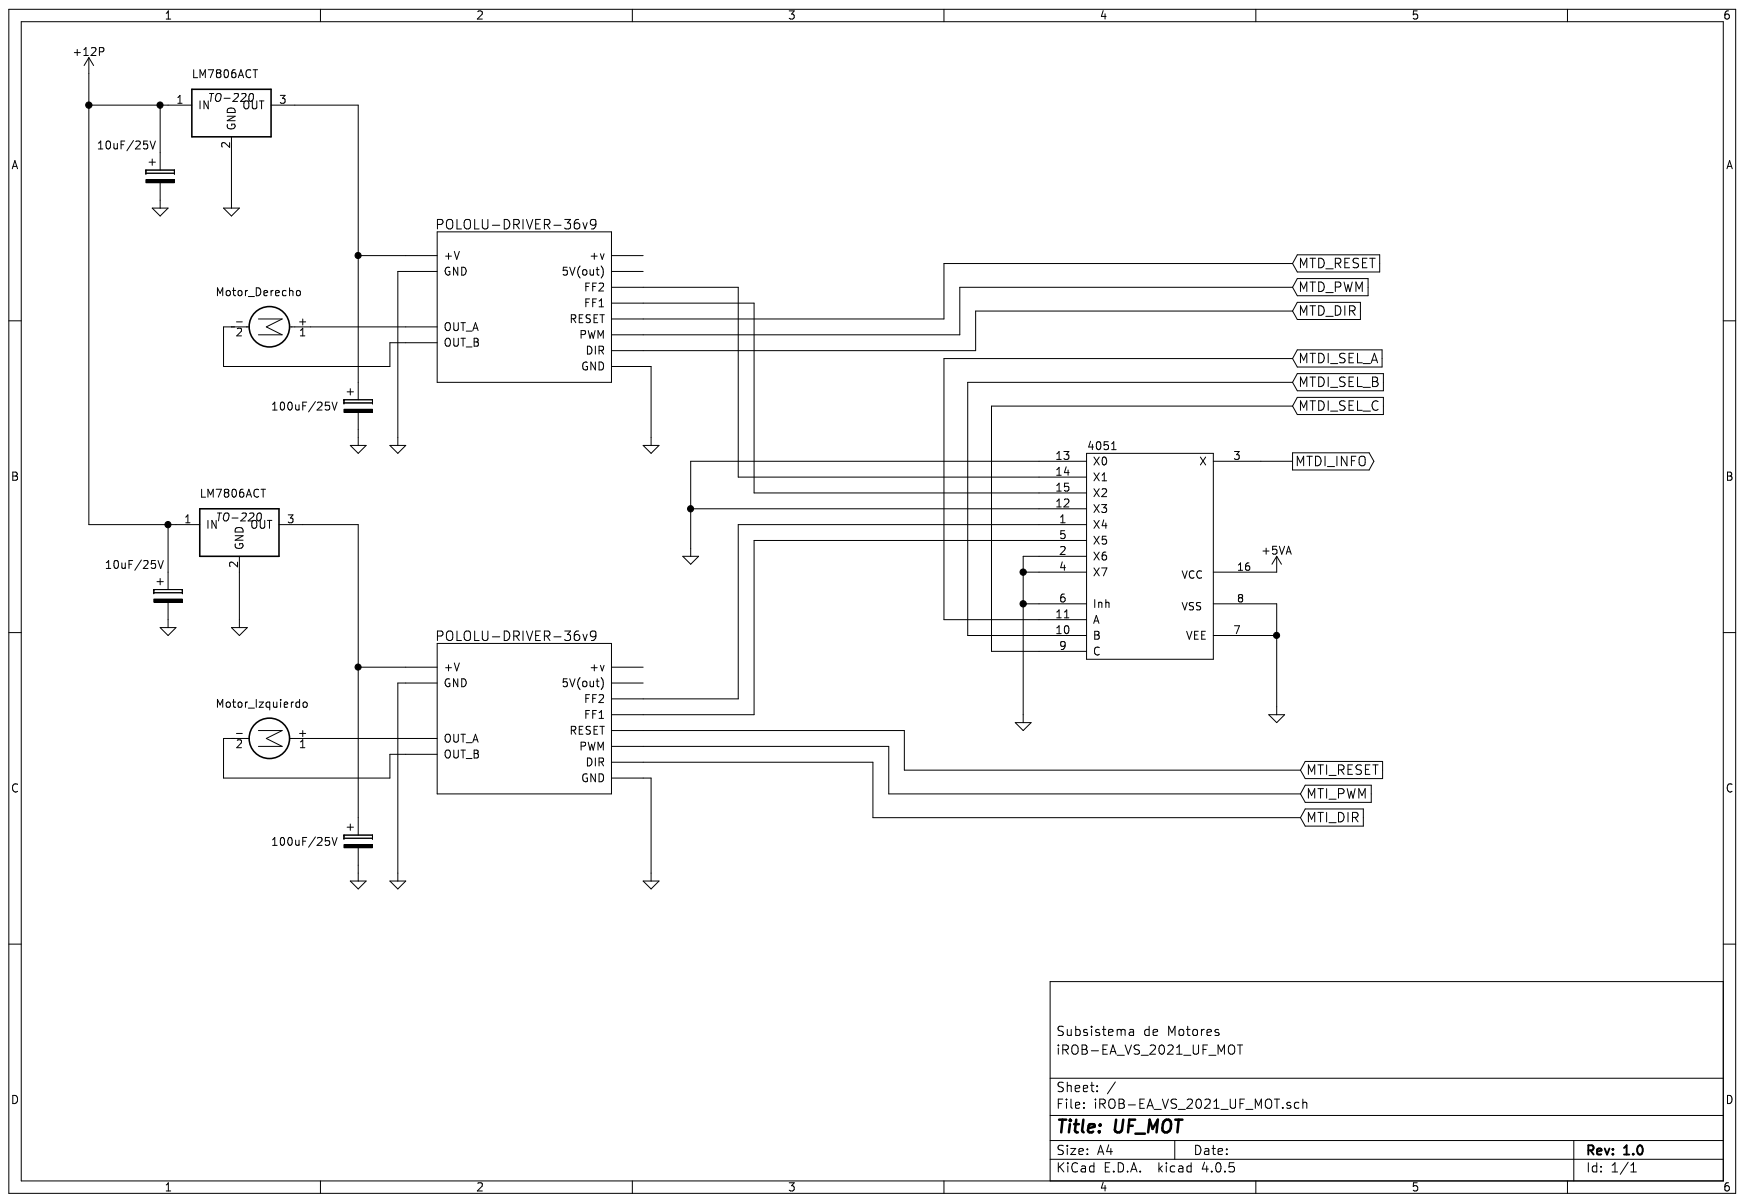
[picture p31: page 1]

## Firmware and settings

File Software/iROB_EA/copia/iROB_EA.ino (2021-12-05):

//! ---------------------------------------------------------
//!
//! @mainpage 
//!                 
//! @brief   Proyecto: iROB-EA
//! @date    Fecha:    Enero 2021
//! @author  AAL
//!
//! @remarks Hardware Arduino MEGA 2560\n
//!
//! @version Versión de SW 1.0
//! @version Versión de IDE Arduino: 1.8.12
//!
//! @brief   <b>Leitmotiv:</b>\n
//!          "Toda Bestia necesita un Cerebro...", Dr. Frankenstein, en su laboratorio\n
//!          "¡Larga y próspera vida!.", Sr. Spock\n
//!
//! ---------------------------------------------------------

//! ---------------------------------------------------------
//!
//! @brief   Funcionalidad:  Modulo principal de la Aplicacion
//!
//! @warning REVISADO --/--/----      
//! ---------------------------------------------------------

#include <Arduino.h>
#include <stdlib.h>
#include <WString.h> 
#include <avr/pgmspace.h>
#include <Wire.h>
#include <Servo.h>
#include <EEPROM.h>
#include <LedDisplay.h>
#include "iROB_EA.h"
#include "UF_SYS.h"
#include "MOTOR_FDS5672.h"
#include "SENSOR_USS.h"
#include "SENSOR_GPS.h"
#include "SENSOR_EMC.h"
#include "SENSOR_RAZOR.h"
#include <Gescom_MEGA2560_V3.h>
#include <Gescom_MEGA2560_V3_CMD.h>


// ---------------------------------------------------------
//
//         Definicion de Clases y variables GLOBALES
//
//
// . uf_sys       Objeto de manejo de  funcionalidades basicas
// . mDer         Objeto de manejo del motor derecho
// . mIzq         Objeto de manejo del motor izquierdo
// . myDisplay    Objeto para manejear el display de estado
// . sensor_USS   Objeto para manejo de los sensores de US
// . sensor_EMC   Objeto para manejo de la estacion climatica
// . sensor_GPS   Objeto para manejo del GPS
// . sensor_RAZOR Objeto para manejo del RAZOR
// . sensor_mlx   Objeto para manejar el sensor MLX90614
// . rtc          Objeto para manejar el reloj de tiempo real 
// . gc           Objeto que implementa el gestor de comandos
//
// . GLOBAL_FlgDebug       Flag para control del modo DEBUG
// . GLOBAL_FlgStatusPC    Flag con el estado del PC      
// . GLOBAL_Timer_Ctrl_PC  Timer asociado a los procesos de
//                         encendido/apagado del PC
// ---------------------------------------------------------

UF_SYS            uf_sys    = UF_SYS();                            // Implementa la funcionalidad relacionada con la UF_SYS

MOTOR_FDS5672     mDer      = MOTOR_FDS5672( PIN_HW_MTD_DIR ,      // Implementa el control del motor derecho
                                             PIN_HW_MTD_RST ,
                                             PIN_HW_MTD_PWM 
                                           );                   

MOTOR_FDS5672     mIzq      = MOTOR_FDS5672( PIN_HW_MTI_DIR ,      // Implementa el control del motor izquierdo
                                             PIN_HW_MTI_RST ,
                                             PIN_HW_MTI_PWM 
                                           );                   

LedDisplay        myDisplay = LedDisplay( PIN_HW_HCMS_DATA  ,      // Implementa el control del display
                                          PIN_HW_HCMS_RS    ,
                                          PIN_HW_HCMS_CLK   ,
                                          PIN_HW_HCMS_CE    ,
                                          PIN_HW_HCMS_RESET ,
                                          4
                                        );                     
                                        
SENSOR_USS       sensor_USS = SENSOR_USS( PIN_HW_USR_DER_TRIGGER , // Implementa el control de los sensores de deteccion de objetos
                                          PIN_HW_USR_IZQ_TRIGGER ,
                                          PIN_HW_USR_DER_ECHO    ,
                                          PIN_HW_USR_IZQ_ECHO    ,
                                          PIN_HW_SUPERFICIE
                                        );         
SENSOR_EMC      sensor_EMC = SENSOR_EMC( PIN_HW_SEN_MET_LUZ);      // Implementa el control de los sensores de la estacion climatica                                                    
SENSOR_GPS      sensor_GPS;                                        // Implementa el modulo de GPS                                        
SENSOR_RAZOR    sensor_RAZOR;                                      // Implementa el modulo de sensores AHRS                                        

GESCOM3           gc        = GESCOM3( IDE_SERIAL_0        ,
                                       false               ,
                                       IDE_DISPOSITIVO_R00 ,
                                       IDE_SERIAL_TRX_PC
                                     );                            // Gestor de comandos

byte              GLOBAL_FlgDebug;                                 // Flag global que indica si se deben generar trazas por el puerto de Debug o no
byte              GLOBAL_FlgStatusPC;                              // Flag para control del proceso de encendido/Apagado                   
byte              GLOBAL_FlgModoAvance;                            // Flag que indica el modo de avance, ver defines IDE_MODO_AVANCE_xx                  
byte              GLOBAL_FlgModoAvanceEvento;                      // Flag que indica eventos detectados cuando la variable GLOBAL_FlgModoAvance = IDE_MODO_AVANCE_CON_PROTECCION
unsigned long int GLOBAL_Timer_Ctrl_PC;                            // Timer asociado a los procesos de encendido/apagado del PC
int               GLOBAL_Timer_DispD_PC;                           // Timer asociado a los procesos de encendido/apagado del PC, para mostrar en el display  
int               GLOBAL_Timer_DispF_PC;                           // Timer asociado a los procesos de encendido/apagado del PC, para mostrar en el display  



// ---------------------------------------------------------
//
// void setup()
//      Funcion para  inicializar  todos  los  sistemas  del
//      iROB-EA 
//
// ---------------------------------------------------------

void setup(void)
{
  // ---------------------------------------------------------
  //
  // ATENCIÓN:
  //
  // . Los pines de control de los motores NO se inicializan
  //   aqui porque ya lo hace el constructor de la clase
  //   MOTOR_FDS5672
  //
  // . Los pines de control del display NO se inicializan
  //   aqui porque ya lo hace el constructor de la clase
  //   ledDisplay
  //
  // . Los pines de control de los sensores de ultrasonidos 
  //   NO se inicializan aqui porque ya lo hace el constructor
  //   de la clase SENSOR_US
  //
  // . El pin PIN_HW_OFF_PETICION es la entrada de INT 0, no 
  //   es necesario inicializar este pin con pinMode
  //
  // ---------------------------------------------------------
 
  // ---------------------------------------------------------
  //
  // Inicializacion de los pines I/O (MODO)
  // Los pines que NO se inicializan expresamente aqui es debido
  // a que se inicializan en los objetos definidos para su 
  // utilizacion, sensor_USS, mDer, MIzq etc
  // ---------------------------------------------------------

  pinMode( PIN_HW_MIC_01       ,INPUT);
  pinMode( PIN_HW_SEN_MET_LUZ  ,INPUT);
  pinMode( PIN_HW_MTDI_INFO    ,INPUT);
  pinMode( PIN_HW_ICC_SENSE_12P,INPUT);
  pinMode( PIN_HW_ICC_SENSE_5VP,INPUT);

  pinMode( PIN_HW_INT_OFF_PETICION,INPUT);
  pinMode( PIN_HW_INT_SQW         ,INPUT);

  pinMode( PIN_HW_POW_CNX_A0,OUTPUT);
  pinMode( PIN_HW_POW_CNX_A1,OUTPUT);
  pinMode( PIN_HW_POW_CNX_A2,OUTPUT);

  pinMode( PIN_HW_DTMF_D0,INPUT);
  pinMode( PIN_HW_DTMF_D1,INPUT);
  pinMode( PIN_HW_DTMF_D2,INPUT);
  pinMode( PIN_HW_DTMF_D3,INPUT);
  pinMode( PIN_HW_DTMF_DV,INPUT);

  pinMode( PIN_HW_CNX_DEBUG,INPUT);

  pinMode( PIN_HW_BAT_N25  ,INPUT);
  pinMode( PIN_HW_BAT_N50  ,INPUT);
  pinMode( PIN_HW_BAT_N75  ,INPUT);
  pinMode( PIN_HW_BAT_N100 ,INPUT);

  pinMode( PIN_HW_SERVO_HOR,OUTPUT);
  pinMode( PIN_HW_SERVO_VER,OUTPUT);
  
  pinMode( PIN_HW_FAN,OUTPUT);
  
  pinMode( PIN_HW_LED_POS ,OUTPUT);
  pinMode( PIN_HW_LED_DER ,OUTPUT);
  pinMode( PIN_HW_LED_IZQ ,OUTPUT);
  pinMode( PIN_HW_LED_FOCO,OUTPUT);

  pinMode( PIN_HW_MTI_DIR,OUTPUT);
  pinMode( PIN_HW_MTI_RST,OUTPUT);
  pinMode( PIN_HW_MTI_PWM,OUTPUT);

  pinMode( PIN_HW_MTD_DIR,OUTPUT);
  pinMode( PIN_HW_MTD_RST,OUTPUT);
  pinMode( PIN_HW_MTD_PWM,OUTPUT);

  pinMode( PIN_HW_MTDI_SEL_A,OUTPUT);
  pinMode( PIN_HW_MTDI_SEL_B,OUTPUT);
  pinMode( PIN_HW_MTDI_SEL_C,OUTPUT);

  pinMode( PIN_HW_POW_PC_1,OUTPUT);

  // ---------------------------------------------------------
  //
  //       !!! Estas variables se INICIALIZAN AQUI !!!
  //
  // ---------------------------------------------------------

  GLOBAL_FlgDebug            = false;  
  GLOBAL_FlgStatusPC         = IDE_STATUS_PC_INI_ON;
  GLOBAL_FlgModoAvance       = IDE_MODO_AVANCE_CON_PROTECCION;
  GLOBAL_FlgModoAvanceEvento = IDE_EVENTO_OK;
  GLOBAL_Timer_Ctrl_PC       = 0L;
  GLOBAL_Timer_DispD_PC      = 0;
  GLOBAL_Timer_DispF_PC      = true;

  
  // ---------------------------------------------------------
  //
  // Inicializacion de variables, objetos Globales y elementos
  //
  //
  // ---------------------------------------------------------

  analogReference(DEFAULT);
  
  // ---------------------------------------------------------
  //
  // ---------------------------------------------------------
     
  Wire.begin();
  mDer.begin();
  mIzq.begin();
  myDisplay.begin();
  myDisplay.setBrightness(15);
  sensor_USS.begin();
  sensor_GPS.begin();
  sensor_EMC.begin();
  sensor_RAZOR.begin();
   
  gc.begin();

  
  // ---------------------------------------------------------
  // Interrupciones:
  //
  // INT 0:    Boton Power OFF
  // Funcion:  INT_power_OFF()
  // Variable: GLOBAL_FlgPower_OFF
  //           Variable actualizada por esta funcion
  //
  // INT 1:    Señal generada desde el RTC
  // Funcion:  INT_rtc_SQW()
  // 
  // ---------------------------------------------------------
  
  attachInterrupt(0, INT_power_OFF, RISING);
  attachInterrupt(1, INT_rtc_SQW  , RISING);
     
  // ---------------------------------------------------------
  //
  //        Inicializacion de puertos serie
  //
  // . Serial0 Gestor de comandos, se inicializa en gc->begin()
  //           Comunicacion entre Arduino y PC
  // . Serial1 GPS  , se inicializa en sensor_GPS.begin()
  // . Serial2 RAZOR, se inicializa en sensor_RAZOR.begin()
  // . Serial3 9600 , puerto de DEBUG, 9600
  //
  // ---------------------------------------------------------
  
  Serial3.begin(IDE_SERIAL_TRX_DEBUG);   // Puerto de DEBUG, ver comentario de la variable GLOBAL_FlgDebug
    
 

  // ---------------------------------------------------------
  //                        IMPORTANTE
  // !!! NO mover de aqui estas inicializaciones
  // Para  version  Funcional, comentar  todas  las lineas que 
  // puedan aparecer debajo de este comentario y dejar SOLO:
  //
  //       uf_sys.begin();
  //
  // ---------------------------------------------------------  
 
  uf_sys.begin();                                          

  // ---------------------------------------------------------  
  // Utilidad para escanear el bus I2C
  // DESCOMENTAR para probar los sensore conectados por I2C
  // ---------------------------------------------------------  
  
  // UTIL_Scanner_I2C();

  // ---------------------------------------------------------  
  // Atencion:
  // Cuando se instala un  nuevo Arduino MEGA, es  conveniente
  // descomentar  esta  llamada  UNA SOLA  VEZ para iniciar la
  // Variable EEPROM a  un  valor  conocido, despues  se  DEBE 
  // dejar comentada
  // ---------------------------------------------------------  
  
  // uf_sys.set_NUM_RC(1);

     
 }





// ---------------------------------------------------------
//
// void loop()
//      Funcion principal para mantener funcionando iROB-EA
//    
// ---------------------------------------------------------

void loop(void)
{
  
  // ---------------------------------------------------------
  // Actualizacion de Timers etc de uf_sys
  // ---------------------------------------------------------
  
  uf_sys.timers();
  
 
  // -------------------------------------------------------
  //
  //                BLOQUE GENERAL DE PROGRAMA
  //
  // -------------------------------------------------------
                    
  // -------------------------------------------------------
  //
  //                    GESTOR DE COMANDOS
  //
  // La funcion exeGesComando ejecuta el gestor de comandos.
  // Si se ha recibido algo en el puerto serie lo  procesa y
  // envia el resultado obtenido.
  // TODAS las funciones asociadas a comandos se  encuentran 
  // en el fichero iROB-EA_CMD.ino
  //
  // Si no se ha recibido nada retorna inmediatamente.
  //
  // Esta funcion retorna:
  // . IDE_BUFF_RX_OK    Se ha recibdo algo valido ( un 
  //                     comando y se ha ejecutado )
  // . IDE_BUFF_RX_ER    Se ha recibido algo erroneo. 
  // . IDE_BUFF_RX_VACIO NO se ha recibido nada
  //
  // Estos defines se encuentran en Gescom_MEGA2560_V3.h
  //
  // -------------------------------------------------------
       
  gc.exeGesComando();

  // -------------------------------------------------------
  //
  //       Proceso de encendido/apagado/Bucle activo
  //
  // - Si el proceso de encendido finaliza correctamente:
  //   GLOBAL_FlgStatusPC = IDE_STATUS_PC_OK = procesoActivo()
  //
  // - Si el proceso de apagado se solicita  actuando  sobre
  //   el pulsador: 
  //   GLOBAL_FlgStatusPC = IDE_STATUS_PC_INI_OFF
  //
  // -------------------------------------------------------

  switch( GLOBAL_FlgStatusPC )
        {
          case ( IDE_STATUS_PC_INI_ON ):
               { // ----------------------------------------
                 //    El PC esta apagado, se acaba de
                 //          arrancar el Robot
                 //
                 // Se inicia el proceso de encendido.
                 // La funcion pc_ON() inicia el encendido y
                 // cambia el valor de GLOBAL_FlgStatusPC  a
                 // GLOBAL_FlgStatusPC = IDE_STATUS_PC_START
                 // ----------------------------------------
                 FNG_DisplayMsgPROGMEM(IDE_MSG_DISPLAY_WAIT,0);                 
                 pc_ON();
                 break;
               }
          case ( IDE_STATUS_PC_START ):
               { // ----------------------------------------
                 //         El PC esta arrancando
                 // Temporiza esperando respuesta  desde  el
                 // PC.
                 //
                 // . Si el PC  se  inicializa correctamente
                 //   se recibira un comando desde el  PC en
                 // la funcion de comandos cmd_Comando_C_STPC()
                 // con el cnv_Param01 = IDE_PARAM_ACT y esa
                 // funcion cambiara el estado de la 
                 // variable 
                 // GLOBAL_FlgStatusPC =  IDE_STATUS_PC_ON
                 //
                 // . Si se agota el tiempo de espera  se pasa
                 // GLOBAL_FlgStatusPC = IDE_STATUS_PC_ON_ERROR
                 //
                 // ----------------------------------------
                 if ( (unsigned long int)(millis()-GLOBAL_Timer_Ctrl_PC)>=IDE_PC_POWER_ON_TIMEOUT  )
                    { // ------------------------------------------
                      // Superado el tiempo maximo  de  espera para
                      // que el PC comunique que  se  ha encendido,
                      // NO se ha recibido desde  el  PC el comando 
                      // #####1001070000E0001 que indicaria  que ha
                      // arrancado correctamente, se indica error y
                      // se cambia GLOBAL_FlgStatusPC
                      // ------------------------------------------
                      FNG_DisplayMsgPROGMEM(IDE_MSG_DISPLAY_ER_000,0);
                      GLOBAL_FlgStatusPC = IDE_STATUS_PC_ON_ERROR;
                    }
                 else
                    { // ------------------------------------------
                      // Muestra tiempo de espera restante
                      // ------------------------------------------
                      displayTimerInicio_PC();
                    } 
                 break;
               }
     
          case ( IDE_STATUS_PC_ON ):
               { // ----------------------------------------
                 //    Se ha recibido desde el PC la
                 //  confirmacion de encendido correcto.
                 // GLOBAL_FlgStatusPC = IDE_STATUS_PC_OK
                 // ----------------------------------------
                 FNG_DisplayMsgPROGMEM(IDE_MSG_DISPLAY_OK ,(IDE_PAUSA_GENERAL*4));
                 FNG_DisplayMsgPROGMEM(IDE_MSG_DISPLAY_CLS,0);
                 GLOBAL_FlgStatusPC = IDE_STATUS_PC_OK;
                 break;
               }
          case ( IDE_STATUS_PC_OK ):
               { // ----------------------------------------
                 // Finalizado  correctamente  el proceso de 
                 // encendido del PC.
                 // Bucle Activo
                 // Aqui  se  deben  incluir todas las cosas
                 // que se deben ejecutar en el modo  normal
                 // de funcionamiento.
                 // ----------------------------------------
                 procesoActivo();
                 break;
               }
          case ( IDE_STATUS_PC_INI_OFF ):
               { // ----------------------------------------
                 //         Se ha pulsado el boton de
                 //             encendido/apagado
                 // Se inicia el proceso de  apagado del  PC
                 // Independientemente  del   resultado  del 
                 // proceso de apagado del PC , se  pasara a
                 // GLOBAL_FlgStatusPC = IDE_STATUS_PC_OFF
                 // ----------------------------------------
                 FNG_DisplayMsgPROGMEM(IDE_MSG_DISPLAY_DOWN,0);
                 pc_OFF();
                 break;
               }          
          case ( IDE_STATUS_PC_DOWN ):
               { // ----------------------------------------
                 // Proceso de apagado del Robot
                 //
                 // ----------------------------------------
                 if ( (unsigned long int)(millis()-GLOBAL_Timer_Ctrl_PC)>=IDE_PC_POWER_OFF_TIMEOUT  )
                    { // ------------------------------------------
                      // Superado el  tiempo  maximo de espera para
                      // detectar el apagado del PC. 
                      // Se indica error y se cambia GLOBAL_FlgStatusPC
                      // para apagar fisicamente el  Robot , aunque 
                      // el PC no se haya apagado correctamente
                      // ------------------------------------------
                      FNG_DisplayMsgPROGMEM(IDE_MSG_DISPLAY_ER_001,(IDE_PAUSA_GENERAL*5));
                      GLOBAL_FlgStatusPC = IDE_STATUS_PC_OFF;
                    }
                 else
                    { // ------------------------------------------
                      // Mide la corriente consumida por el PC para
                      // detectar cuando se apaga
                      // ------------------------------------------
                      if ( getIcc5VP()==false )
                         { // ------------------------------------------
                           // La corriente medida con el sensor asociado
                           // a la alimentacion del PC determina  que se
                           // ha apagado.
                           // Se indica ok y se cambia GLOBAL_FlgStatusPC
                           // para apagar fisicamente el Robot
                           // ------------------------------------------
                           FNG_DisplayMsgPROGMEM(IDE_MSG_DISPLAY_OK,(IDE_PAUSA_GENERAL*5));
                           GLOBAL_FlgStatusPC = IDE_STATUS_PC_OFF;
                         }
                    }

                 break;
               }
          case ( IDE_STATUS_PC_OFF ):
               { // ----------------------------------------
                 // Apagado fisico del Robot -)
                 // ----------------------------------------
                 uf_sys.power_OFF();
                 break;
               }
          case ( IDE_STATUS_PC_ON_ERROR ):
               { // ----------------------------------------
                 // El PC no ha  podido  encenderse, se debe
                 // dejar la alimentacion conectada para que
                 // desde el exterior , via teclado/Raton se
                 // pueda determinar el fallo
                 // ----------------------------------------

 
                 break;
               }     
        }
  
}



// ---------------------------------------------------------
//
// void pc_ON(void)
// Efectua las operaciones necesarias para  encender el PC y
// cambia el estado de la variable global GLOBAL_FlgStatusPC
// al valor: 
//    GLOBAL_FlgStatusPC = IDE_STATUS_PC_START
//
// ---------------------------------------------------------
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

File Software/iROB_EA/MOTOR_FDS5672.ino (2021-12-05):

// ---------------------------------------------------------
//
// Proyecto:       iROB-EA
// Version:        1.0
// Fichero:        MOTOR_FDS5672.ino
// Autor:
// Hardware:       Arduino MEGA 2560
// Fecha:          Enero 2021
//
// Funcionalidad:  Implmentacion de la clase MOTOR_FDS5672
//
// Notas:          REVISADO 27/04/2021  
//
// ---------------------------------------------------------

#include "MOTOR_FDS5672.h"




// ---------------------------------------------------------
//
// MOTOR_FDS5672::MOTOR_FDS5672( int pin_DIR ,
//                               int pin_RST ,
//                               int pin_PWM 
//                             )
//         Constructor
//
// ---------------------------------------------------------

MOTOR_FDS5672::MOTOR_FDS5672(int pin_DIR,int pin_RST,int pin_PWM)
{
   pinDIR = pin_DIR;        
   pinRST = pin_RST;
   pinPWM = pin_PWM;
}




// ---------------------------------------------------------
//
// void MOTOR_FDS5672::begin(void)
//         
//
// ---------------------------------------------------------

void MOTOR_FDS5672::begin (void)
{
  
   pinMode(pinDIR,OUTPUT); // Motor derecho, Direccion
   pinMode(pinRST,OUTPUT); // Motor derecho, Reset

   lVelocidad = false;
   velocidad(IDE_MOTOR_FDS5672_VEL_DEFECTO);
   paro();
}




// ---------------------------------------------------------
//
// void MOTOR_FDS5672::avance (void)
//         
//
// ---------------------------------------------------------

void MOTOR_FDS5672::avance (void)
{
  modo = IDE_MOTOR_FDS5672_AVANCE;
  digitalWrite(pinDIR,LOW); 
  setValores();
}



// ---------------------------------------------------------
//
// void MOTOR_FDS5672::retroceso (void)
//         
//
// ---------------------------------------------------------

void MOTOR_FDS5672::retroceso (void)
{
  modo = IDE_MOTOR_FDS5672_RETROCESO;
  digitalWrite(pinDIR,HIGH); 
  setValores();
}



// ---------------------------------------------------------
//
// void MOTOR_FDS5672::paro (void)
//         
//
// ---------------------------------------------------------

void MOTOR_FDS5672::paro (void)
{
  modo = IDE_MOTOR_FDS5672_PARO;
  digitalWrite(pinRST,LOW); 
}



// ---------------------------------------------------------
//
// void MOTOR_FDS5672::velocidad(byte valor)
//         
//
// ---------------------------------------------------------

void MOTOR_FDS5672::velocidad(byte valor)
{
    
  if ( lVelocidad==false )
     { // ------------------------------------
       // La velocidad NO esta limitada
       // ------------------------------------
       vVelocidad = valor;
     }
  else
     { // ------------------------------------
       // La velocidad limitada
       // ------------------------------------
       vVelocidad = IDE_MOTOR_FDS5672_VEL_LIMITADA;
     }

  analogWrite(pinPWM,vVelocidad);  
  setValores();

}



// ---------------------------------------------------------
//
// void MOTOR_FDS5672::limitarVelocidad(byte modo)
//         
//
// ---------------------------------------------------------

void MOTOR_FDS5672::limitarVelocidad(byte modo)
{
  lVelocidad = modo;
  if ( lVelocidad==true )
     { // -----------------------------------------------------
       // Se limita la velocidad, actualiza la velocidad en los 
       // motores
       // -----------------------------------------------------
       velocidad(IDE_MOTOR_FDS5672_VEL_LIMITADA);
     }
}



// ---------------------------------------------------------
//
// void MOTOR_FDS5672::setValores(void)
//         
//
// ---------------------------------------------------------

void MOTOR_FDS5672::setValores(void)
{
  digitalWrite(pinRST,LOW); 
  delayMicroseconds(IDE_MOTOR_FDS5672_PULSO_VAL);
  digitalWrite(pinRST,HIGH); 
}

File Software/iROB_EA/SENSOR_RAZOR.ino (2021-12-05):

// ---------------------------------------------------------
//
// Proyecto:       iROB-EA
// Version:        1.0
// Fichero:        SENSOR_RAZOR.ino
// Autor:
// Hardware:       Arduino MEGA 2560
// Fecha:          Enero 2021
//
// Funcionalidad:  Implmentacion de la clase SENSOR_RAZOR
//
//                 IMPORTANTE:
//                 Todos los comandos que se intercambian con
//                 el modulo 9DOF Razor IMU estan definidos y
//                 explicados por los autores del firmware de
//                 dicho modulo en el fichero Razor_AHRS.ino.
//                 Es necesario  ver  esos  comentarios para 
//                 entender como funciona el modulo. 
//
// Notas:          REVISADO 
//
// ---------------------------------------------------------

#include "SENSOR_RAZOR.h"




// ---------------------------------------------------------
//
// SENSOR_RAZOR::SENSOR_RAZOR( void )  
//             Constructor
//
// ---------------------------------------------------------

SENSOR_RAZOR::SENSOR_RAZOR(void)
{
  
     
}



// ---------------------------------------------------------
//
// void SENSOR_RAZOR::begin(void)
//
// ---------------------------------------------------------

void SENSOR_RAZOR::begin(void)
{
  
  Serial2.begin(IDE_SERIAL_TRX_RAZOR); // Programa la velocidad del puerto para comunicarse con el modulo
  Serial2.write("#oe0");               // Comando del modulo 9DOF Razor IMU que deshabilita los errores de salida
  Serial2.write("#o0");                // Comando del modulo 9DOF Razor IMU que deshabilita la salida continua de informacion desde el modulo
  Serial2.write("#ot");                // Comando del modulo 9DOF Razor IMU que indica salida de datos en formato TEXTO
  Serial2.write("#osct");              // Comando del modulo 9DOF Razor IMU que indica Salida de datos SENSORES CALIBRADOS de los 9 ejes
  Serial2.flush();
    
  sBuffFrame[0]='\0';
  
  
}


// ---------------------------------------------------------
//
// byte SENSOR_RAZOR::getFrameSensor(char* sensorID)
//
// ---------------------------------------------------------

byte SENSOR_RAZOR::getFrameSensor(char* sensorID)
{
 
  byte   nReintentos;
  byte   resultado;
  byte   nCar1;
  byte   nCar2;
  String sAux; 
  
  
  resultado     = true;
  nReintentos   = 0;
  sBuffFrame[0] = '\0';
  
  while ( true )
        {
          if ( Serial2.available()>0 )
             {
               sAux = Serial2.readStringUntil('\n');
               if (sAux.indexOf(sensorID,0)!=-1 )
                  { 
                    nCar1 = strlen(sensorID) + 1;
                    nCar2 = sAux.length();                  
                    strcpy(sBuffFrame,sAux.substring(nCar1,nCar2).c_str());
                    if ( testSFrame()==true )
                       { // --------------------------------
                         // El formato es correcto
                         // --------------------------------
                         break;
                       }
                  }
             }
          else
             {
               Serial2.write("#f");
               delayMicroseconds(IDE_MAX_FRAME_DELAY);
               if ( nReintentos>=IDE_NUM_FRAME_REINTENTOS )
                  {
                    resultado = false;
                    break;
                  }
               else
                  {
                    nReintentos++;        
                  }
             }
        }
        
  Serial2.flush();   
 
  if ( resultado==false )
     { // ------------------------------------
       // No se han podido recuperar los datos
       // ------------------------------------
       sBuffFrame[0] = '\0';
     }
     
  return ( resultado );
}



// ---------------------------------------------------------
//
// byte SENSOR_RAZOR::testSFrame(void)
//
// ---------------------------------------------------------

byte SENSOR_RAZOR::testSFrame(void)
{
  byte resultado;
  byte nComas;
  byte indCar;
  byte numCar;
  

  resultado = true;
  nComas    = 0;
  numCar    = strlen(sBuffFrame);

  for ( indCar=0;indCar<numCar;indCar++ )
      { // ------------------------------------
        // Recorre el string para comprobar que 
        // tiene el  formato correcto, segun la
        // documentacion del sensor es:
        // valores x,y,z
        // ------------------------------------
        if ( sBuffFrame[indCar]==',' )
           {
             nComas++; 
           }
      }

  if ( nComas!=2 )
     { // ----------------------------------
       // El formato no es correcto
       // ----------------------------------
       resultado = false;
     }
  else
     { // ----------------------------------
       // Comprobaciones adicionales
       // ----------------------------------       
       switch( sBuffFrame[numCar-1] )
             {
               case( '\r' ):
                   { sBuffFrame[numCar-1] = '\0';
                     break;
                   }
               case( ',' ):
                   { 
                     resultado = false;
                     break;
                   }
             }
     }
     
  return( resultado );
}



// ---------------------------------------------------------
//
// char* SENSOR_RAZOR::getFrameAcc(void)
//
// ---------------------------------------------------------

char* SENSOR_RAZOR::getFrameAcc(void)
{

  getFrameSensor(IDE_SENSOR_ACC);
  
  if ( GLOBAL_FlgDebug==true )
     {
       Serial3.println(sBuffFrame);
     }
      
  return ( sBuffFrame );
}



// ---------------------------------------------------------
//
// char* SENSOR_RAZOR::getFrameMag(void)
//
// ---------------------------------------------------------

char* SENSOR_RAZOR::getFrameMag(void)
{

  getFrameSensor(IDE_SENSOR_MAG);
  
  if ( GLOBAL_FlgDebug==true )
     {
       Serial3.println(sBuffFrame);
     }
      
  return ( sBuffFrame );
}



// ---------------------------------------------------------
//
// char* SENSOR_RAZOR::getFrameGyr(void)
//
// ---------------------------------------------------------

char* SENSOR_RAZOR::getFrameGyr(void)
{

  getFrameSensor(IDE_SENSOR_GYR);
  
  if ( GLOBAL_FlgDebug==true )
     {
       Serial3.println(sBuffFrame);
     }
  
  return ( sBuffFrame );
}

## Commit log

2016-02-07 Versio Inicial V1.0.0
    [Arduino_MEGA2560_ref.brd, Arduino_MEGA2560_ref.sch]
2016-02-10 Añadido sw especifico para Arduino
2016-02-15 Zip de SW versión actual
2016-03-03 SW: Clase SENSOR_US
2016-03-13 Cambio Arduino IDE 1.6.4
2016-03-13 Cambio Arduino IDE 1.6.4, quitadas copias
2016-03-14 Implemetacion Ctrl LEDs
2016-03-17 SW Implementacion Leds
2016-03-17 SW Gestion de Baterias
2016-03-20 SW Control leds OK
2016-03-22 SW Actualizacion Sensores
2016-04-03 HW Senal carga activa de bateria
2016-04-04 SW Comandos de Movimiento
2016-04-06 SW con Problemas de carga
    [MOTOR_FDS5672.h, MOTOR_FDS5672.ino, UF_SYS.h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]
2016-04-08 SW revision general de codigo
2016-04-12 Control de Motores
2016-04-13 SW control ON/OFF Motores
2016-04-18 SW Comandos Motores
2016-05-06 Incorporacion al proyecto de Docxygen
2016-11-16 Añadida informacion ficheros CAD y Cargador Inhalambrico
    [iROB-EA-Cargador_V1.FCStd, iROB-EA-Cargador_V1.stl, iROB-EA-Tapa_A_01.FCStd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]
2016-11-28 Actualizacion Ficheros CAD
    [iROB-EA-Cargador_E_V1.FCStd, iROB-EA-Cargador_E_V1.stl, iROB-EA-Cargador_R_V1.FCStd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]
2016-12-02 Texturas en SW
    [iROB-EA-Cargador_E_V1.FCStd, iROB-EA-Cargador_E_V1.stl]
2016-12-07 Fotos Adicionales
    [iROB-EA-Cargador_E_V1.FCStd, iROB-EA-Cargador_E_V1.stl, iROB-EA-Tapa_B_02.FCStd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]
2016-12-23 Actualizavion Ficheros CAD
    [iROB-EA-Cargador_R_V1.FCStd, iROB-EA-Cargador_R_V1.stl, iROB-EA-Cargador_R_V2.FCStd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]
2017-02-01 Ficheros CAD y Fotos 201701
    [iROB-EA-Cargador_RT_V1 - copia.FCStd, iROB-EA-Cargador_RT_V1.FCStd, iROB-EA-Cargador_RT_V1.stl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]
2021-04-26 Actualizacion general
    [iROB-EA_SensorSuelo.FCStd, iROB-EA_SensorSuelo.stl, iROB-EA_VS_2021_UF_ENE.sch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]
2021-11-07 Actualizacion 2021
    [Arduino_MEGA2560_ref.brd, Arduino_MEGA2560_ref.sch, iROB-EA_Caja_Adaptador_DEBUG.FCStd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]
2021-11-25 Actualizacion python
    [UF_PC.kicad_pcb, UF_PC.sch, iROB-EA_VS_2021_UF_ENE.sch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]
2021-12-05 Actualizado proceso ON/OFF
    [UF_PC.sch]
